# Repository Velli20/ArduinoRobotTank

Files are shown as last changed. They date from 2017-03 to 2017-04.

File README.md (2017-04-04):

# ArduinoRobotTank

CAD Assembly

Fully 3D-printable robot for Arduino Mega/Uno/Due Controller Board. Designed to fit up to 2 pcs of Arduino shields on top of the controller board.

## Parts to print

- Chassis_top.stl
- Chassis_bottom.stl
- Motor_mount_plate.stl (2 pcs)
- Wheel_cover_14_t.stl (2 pcs)
- Track_wheel_14t.stl (6 pcs)
- Motor_cover.stl (2 pcs)
- Tank_link_pin.stl (68 pcs)
- tank_link.stl (68 pcs)
- Front_cover_for_HC_SR04.stl (2 pcs)

## Optional parts to print

- Chassis_fastener_holder.stl (29 pcs). These are for holding chassis nuts in place so it is easier to assemble the robot.

## Fasteners

- ISO10642 Screw M3x8 40 pcs
- ISO14579 Screw M3x12 8 pcs
- ISO14579 Screw M3x25 4 pcs
- ISO4032 Nut M3 46 pcs

## Fasteners for LCD:

- ISO4762 Screw M2x8 4 pcs
- ISO4032 Nut M2 4 pcs

## Fasteners for Ultrasonic HC-SR04 Distance Sensor:

- ISO4762 Screw M2x8 8 pcs
- Nylon Spacers M2x5 8 pcs
- ISO4762 Screw M2x12 8 pcs

## Electronics

- 2x geared DC motors
- Arduino DUE/Mega/UNO Controller Board
- L298P Motor Shield R3
- 7.4 V LiPo battery

## Optional electronics

- ESP8266 WiFI Development Board 
- SSD1306 0.96" I2C 128X64 OLED LCD
- Ultrasonic HC-SR04 Distance Sensor 2 pcs
- HC-05 Bluetooth module 

## Code example

Usage of the skid steering algorithm:

```C++
#define MOTOR_SPEED_MAX 255     // Define max speed
#define MOTOR_SPEED_MIN -255    // Define min speed

SkidSteer skidSteer;

void loop() {
    skidSteer.move(255, 100);   // Move at speed 255 in x direction and 100 at y direction
}
```

## Images

Printed
Printed

## Android app

You can find precompiled apk in Android-App folder. With this app you can create "programs" that can be executed over Bluetooth connection. It also has a serial console and a "joystick" manual control.

Screenshots

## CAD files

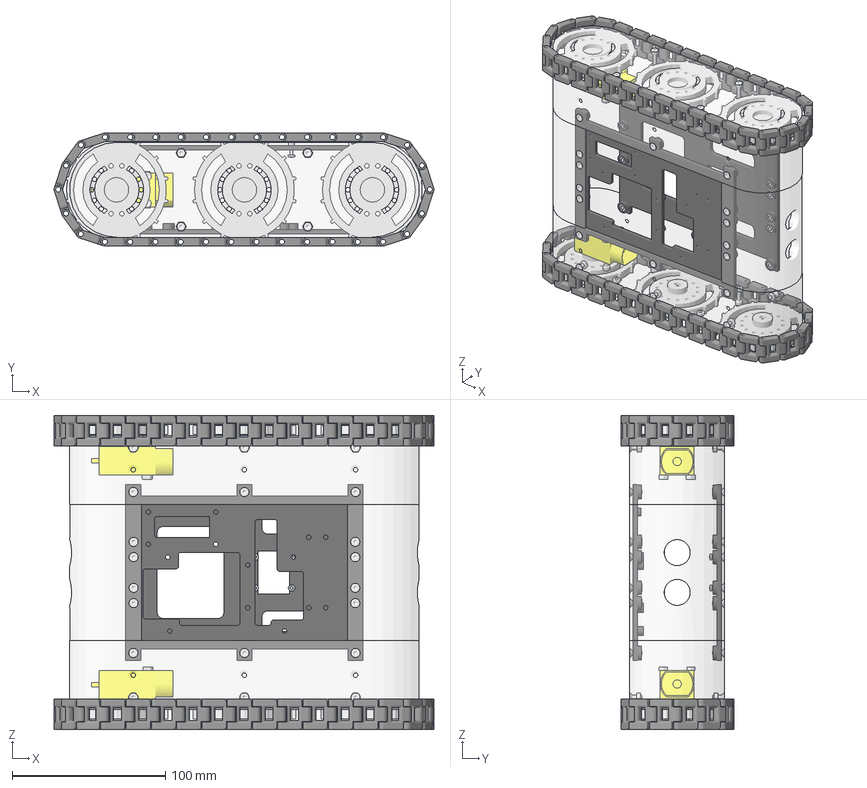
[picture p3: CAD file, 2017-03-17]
Assembly.FCStd
247.9 x 73.8 x 205.0 mm
M3x8-Screw
M3x8-Screw001
M3x8-Screw002
M3x8-Screw003
M3x8-Screw004
M3x8-Screw005
M3-Nut015
M3-Nut014
M3-Nut013
M3-Nut012
M3-Nut011
M3-Nut010
M3-Nut009
M3x12-Screw
M3x12-Screw001
M3x12-Screw002
M3x12-Screw003
M3-Nut008
M3-Nut007
M3-Nut006
M3-Nut002
(M3.5)-Nut020
(M3.5)-Nut019
(M3.5)-Nut018
(M3.5)-Nut017
M3x12-Screw010
M3x12-Screw008
M3x12-Screw007
M3x12-Screw009
M3x25-Screw001
M3x25-Screw
M3-Nut001
M3-Nut
(M3.5)-Nut012
(M3.5)-Nut011
M3x25-Screw003
M3x25-Screw002
(M3.5)-Nut001
(M3.5)-Nut002
M3x8-Screw010
M3x8-Screw009
(M3.5)-Nut
M3x8-Screw006
M3x8-Screw014
(M3.5)-Nut005
(M3.5)-Nut004
(M3.5)-Nut003
M3x8-Screw016
M3x8-Screw015
M3x8-Screw017
M3x8-Screw023
M3x8-Screw022
M3x8-Screw024
M3x8-Screw027
M3x8-Screw028
(M3.5)-Nut008
(M3.5)-Nut007
(M3.5)-Nut006
M3-Nut018
M3-Nut016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

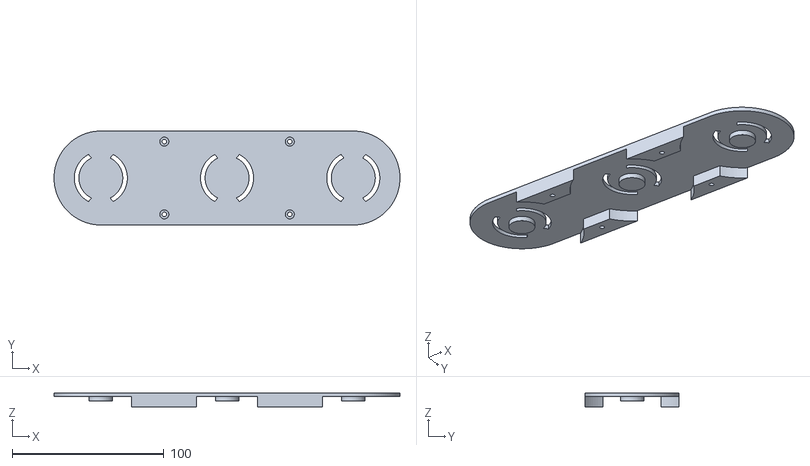
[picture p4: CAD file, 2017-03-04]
STL-files/Wheel_cover_14_t.stl
228.2 x 62.0 x 9.50

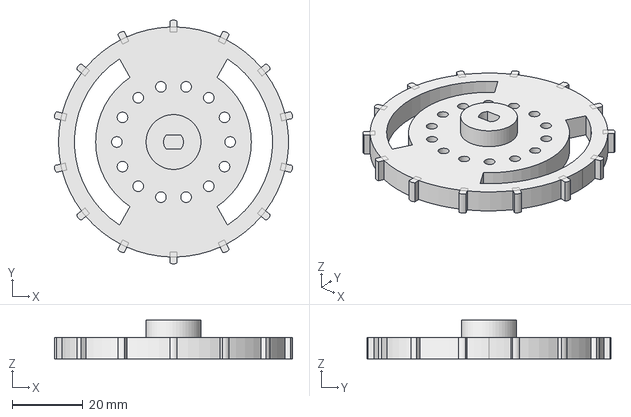
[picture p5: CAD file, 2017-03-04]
CAD-files/Track_wheel_14t_v2.FCStd
67.3 x 68.9 x 11.0 mm

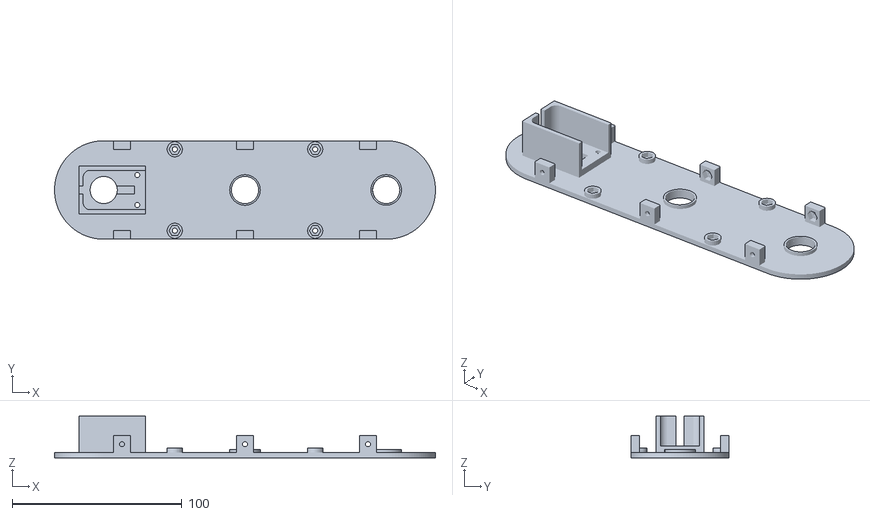
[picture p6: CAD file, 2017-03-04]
STL-files/Motor_mount_plate.stl
224.5 x 58.0 x 24.5

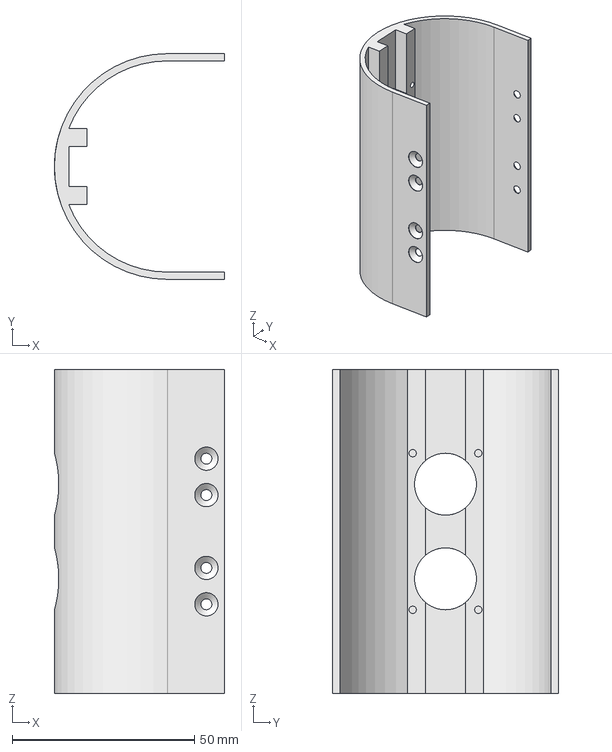
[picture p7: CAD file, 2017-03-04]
CAD-files/Front_cover_with_ultrasonic_distance_sensor_mount.FCStd
46.8 x 62.0 x 89.0 mm

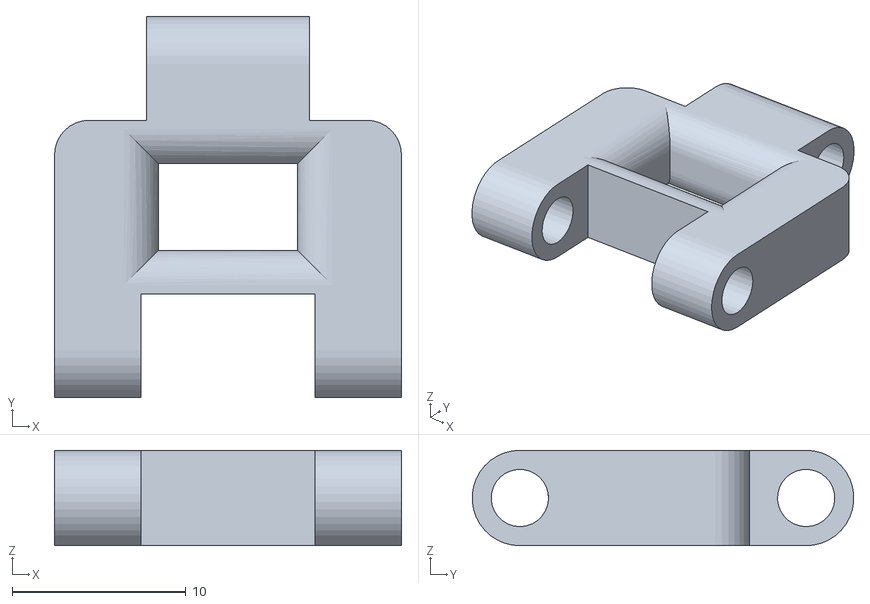
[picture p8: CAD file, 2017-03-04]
STL-files/Tanklink.stl
20.0 x 22.0 x 5.50

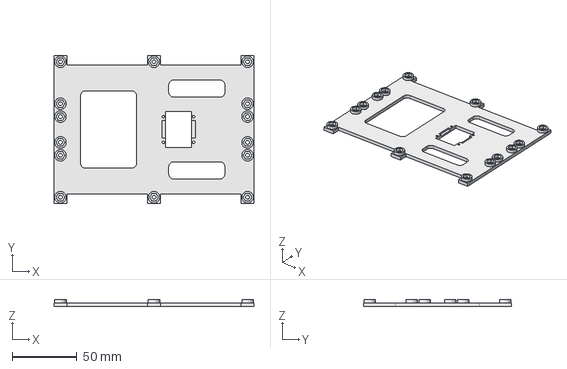
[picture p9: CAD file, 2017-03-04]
CAD-files/Chassis_top.FCStd
155.0 x 115.0 x 5.70 mm

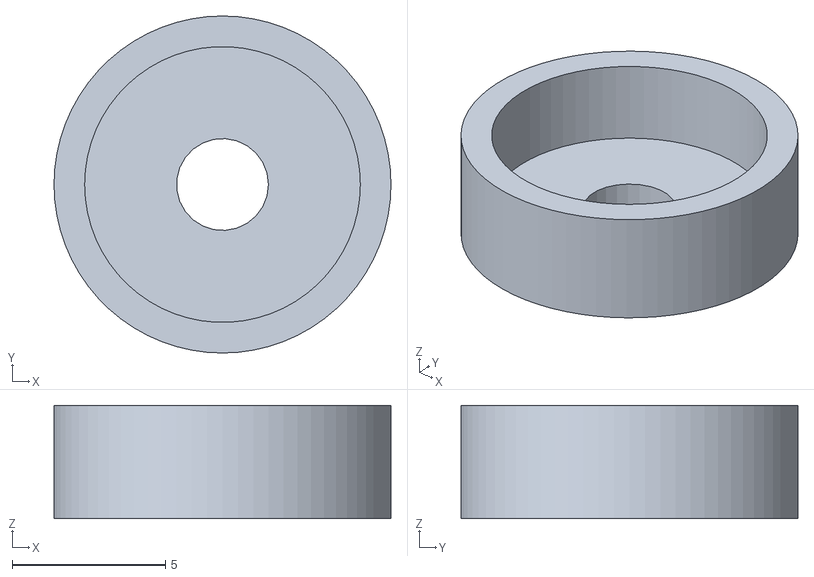
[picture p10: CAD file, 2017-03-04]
STL-files/Chassis_fastener_holder.stl
11.0 x 11.0 x 3.70

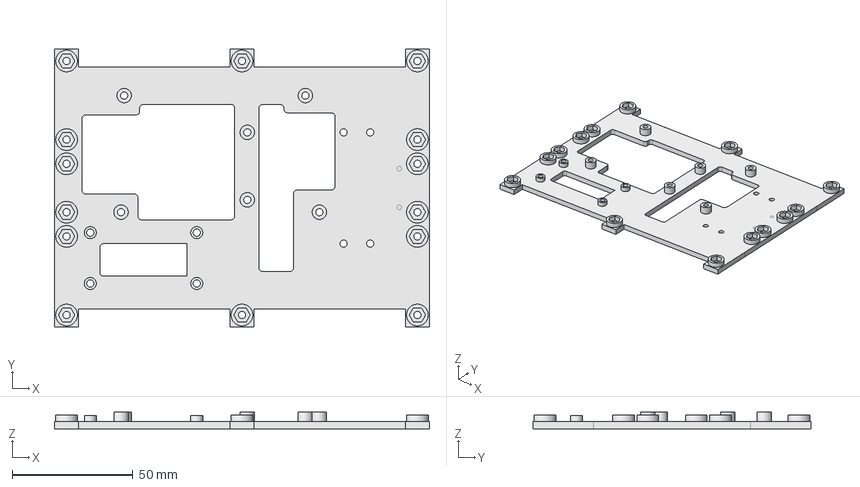
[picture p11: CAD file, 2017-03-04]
CAD-files/Chassis_bottom.FCStd
155.0 x 115.0 x 7.00 mm

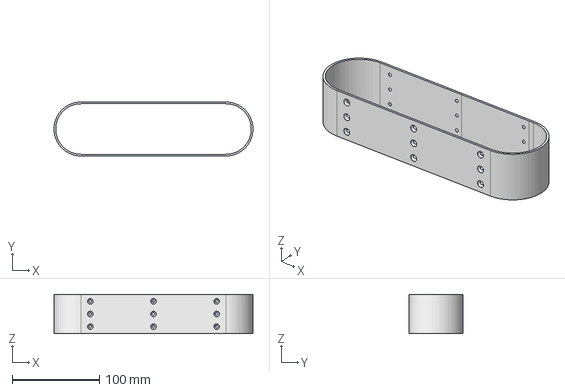
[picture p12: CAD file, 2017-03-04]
CAD-files/Motor_cover.FCStd
228.5 x 62.0 x 45.0 mm

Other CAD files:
CAD-files/Wheel_cover_14_t_v2.FCStd
STL-files/Front_cover_for_HC_SR04.stl
CAD-files/Motor_mount_plate_v2.FCStd
STL-files/Track_wheel_14t.stl
CAD-files/Chassis_nut_holder.FCStd
STL-files/Chassis_bottom.stl
STL-files/Chassis_top.stl
STL-files/Motor_cover.stl

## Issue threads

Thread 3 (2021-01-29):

Question for help

MaxLansing, 2021-01-29:
Hi there,
thx for sharing the project, i'm new to arduino, and i would like to build your rover for the daughter. i have the same parts as per your suggestion, printed all the parts.
But since i am new to the arduino world, and new to programming, i would like to ask if you could share the (working)code with all definitions and maybe a wiring picture if at all possible. At least i could reverse-engineer the mistakes i made and/or see where i am stuck.

thx for great design and the sharing regardless!

Closed 2021-01-30.

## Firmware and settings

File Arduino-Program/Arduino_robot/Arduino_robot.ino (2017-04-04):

#include "skidSteer.h"
#include "configuration.h"
#include <stdio.h>
#include <stdarg.h>


/* Variables */
long lcdLastUpdate = 0;
int speedX = 0;
int speedY = 0;

SkidSteer skidSteer;

/* Function prototypes*/
void updateLCD(void);
void sendResponse(char * response);
void sendResponse(const char * formatter, ...);

/* Put your setup code in this function, to run once: */
void setup() {
  Serial.begin(9600);
  BLUETOOTH_MODULE_SERIAL_PORT.begin(BLUETOOTH_MODULE_BAUD_RATE);
  BLUETOOTH_MODULE_SERIAL_PORT.setTimeout(BLUETOOTH_READ_TIMEOUT);

#ifdef HAS_OLED_LCD
  /* Init OLED display connected at i2c address 0x3C */
  display.begin(SSD1306_SWITCHCAPVCC, 0x3C);
  display.clearDisplay();
  display.setTextSize(1);
  display.setTextColor(WHITE);
#endif /* HAS_OLED_LCD */

  /* Send message to Android console */
  sendResponse("Arduino Tank ready");
  skidSteer.delay(11000);
}

void loop() {

  /* Check if there is data available in Bluetooth Serial Buffer */
  if (BLUETOOTH_MODULE_SERIAL_PORT.available() && !skidSteer.isDelaying()) {
    char command = BLUETOOTH_MODULE_SERIAL_PORT.read();
    long timeReadingStart = millis();
    long value;

    switch (command) {

      /* Commands send by Android app.
         Format: #VALUE where # is the letter prefix and VALUE is an interger 0-255
         Example: X100 == Move in x direction at speed of 100 */

      case 'Y':   /* Command accelerometer tilt in y direction */
      case 'W':   /* Command joystick y-axis*/
        speedY = BLUETOOTH_MODULE_SERIAL_PORT.parseInt();;
        break;

      case 'X':   /* Command accelerometer tilt in x direction */
      case 'A':   /* Command joystick x-axis */
        speedX = BLUETOOTH_MODULE_SERIAL_PORT.parseInt();;
        break;
      case 'D':   /* Command wait or delay */
        value = BLUETOOTH_MODULE_SERIAL_PORT.parseInt();
        sendResponse("Arduino Tank: Delaying for %d ms", value);
        skidSteer.delay(value);
        break;
      case 'N':   /* Command move amount of distance in cm backward */
        value = BLUETOOTH_MODULE_SERIAL_PORT.parseInt();
        sendResponse("Arduino Tank: Moving %d cm backward", value);
        skidSteer.moveDistance((int)value, false);
        break;
      case 'H':   /* Command move amount of distance in cm forward */
        value = BLUETOOTH_MODULE_SERIAL_PORT.parseInt();
        sendResponse("Arduino Tank: Moving %d cm forward", value);
        skidSteer.moveDistance((int)value, true);
        break;
      case 'J':   /* Command rotate counterclockwise amount of degrees */
        value = BLUETOOTH_MODULE_SERIAL_PORT.parseInt();
        sendResponse("Arduino Tank: Rotating %d degrees CCW", value);
        skidSteer.rotate((int)value, true);
        break;
      case 'K':   /* Command rotate clockwise amount of degrees */
        value = BLUETOOTH_MODULE_SERIAL_PORT.parseInt();
        sendResponse("Arduino Tank: Rotating %d degrees CW", 100);
        skidSteer.rotate((int)value, false);
        break;
      case 'S':   /* Command set x speed to 0 and y speed to 0-255 */
        value = BLUETOOTH_MODULE_SERIAL_PORT.parseInt();
        sendResponse("Arduino Tank: Speed set to %d. Max value is set to %d and Min %d", value, MOTOR_SPEED_MAX, MOTOR_SPEED_MIN);
        speedY = value;
        speedX = 0;
        break;
      default:
        sendResponse("Arduino Tank: Unknown command \"%c\"", command);

        break;
    }
  }

  /* Update LCD every 500 ms */
  if (millis() >= (lcdLastUpdate + 100)) {
    updateLCD();
    lcdLastUpdate = millis();
  }

  /* Check that delay function is inactive */
  if (!skidSteer.isDelaying()) {
    skidSteer.move(speedX, speedY);
  }
}




/* Updates content of the OLED LCD if LCD is connected */
void updateLCD() {

#ifdef HAS_OLED_LCD
  char text[40];
  if (skidSteer.isDelaying()) {
    sprintf(text, "Speed Y: %d\nSpeed X: %d\nDelay for: %d ms", speedY, speedX, skidSteer.getRemainingDelayTime());
  } else {
    sprintf(text, "Speed Y: %d\nSpeed X: %d", speedY, speedX);
  }
  display.clearDisplay();
  display.setCursor(0, 5);
  display.print(text);
  display.display();
#endif /* HAS_OLED_LCD */
}

/* Send message to Android App console
   @param formatter: String that contains a format string
   @param values: Additioanl int values reltated to formatter string
*/
void sendResponse(const char * formatter, ...) {
  va_list args;
  va_start(args, formatter);

  char response[80] = {"\0"};
  vsprintf(response, formatter, args);

  BLUETOOTH_MODULE_SERIAL_PORT.write(response);
  BLUETOOTH_MODULE_SERIAL_PORT.write("\r");
  BLUETOOTH_MODULE_SERIAL_PORT.flush();

  va_end(args);

}

/* Send message to Android App console
   @param response: pointer to message to send
*/
void sendResponse(char * response) {
  BLUETOOTH_MODULE_SERIAL_PORT.write(response);
  BLUETOOTH_MODULE_SERIAL_PORT.write("\r");
  BLUETOOTH_MODULE_SERIAL_PORT.flush();
}

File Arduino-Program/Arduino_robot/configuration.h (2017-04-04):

/* Uncomment the following defination if SSD1306 0.96" I2C 128X64 OLED LCD is connected */
/* #define HAS_OLED_LCD */
#define HAS_OLED_LCD
#ifdef  HAS_OLED_LCD
/* Import libraries that are required to communicate with
   the SSD1306 0.96" I2C 128X64 OLED LCD.

   Download the following libraries
   https://github.com/adafruit/Adafruit-GFX-Library
   https://github.com/adafruit/Adafruit_SSD1306
*/
#include <Adafruit_GFX.h>
#include <Adafruit_SSD1306.h>
#include <Wire.h>

#define OLED_RESET 4
Adafruit_SSD1306 display(OLED_RESET);

#endif /* HAS_OLED_LCD */

/* Uncomment the following defination if Ultrasonic HC-SR04 Distance Sensor is connected */
/* #define HAS_ULTRASONIC_DISTANCE_SENSOR */
#ifdef HAS_ULTRASONIC_DISTANCE_SENSOR

/* Import library that is reguired to communicate wit the sensor
   Link to download NewPing library
   http://playground.arduino.cc/Code/NewPing#Download */
#include <NewPing.h>

/* Defines for the ultrasonic distance sensor */
#define PIN_ULTRASONIC_TRIGGER 51                 // Arduino pin tied to trigger pin on the ultrasonic sensor.
#define PIN_ULTRASONIC_ECHO 53                    // Arduino pin tied to echo pin on the ultrasonic sensor.
#define ULTRASONIC_MAX_DISTANCE 200               // Maximum distance we want to ping for (in centimeters)

#endif /* HAS_ULTRASONIC_DISTANCE_SENSOR */

/* Serial port at which bluetooth module is connected.
   Arduino UNO has only one serial port, so change the value to
   Serial and make sure to disconnect the module when uploading the code
   to the Arduino board */
#define BLUETOOTH_MODULE_SERIAL_PORT    Serial2
#define BLUETOOTH_MODULE_BAUD_RATE      57600
#define BLUETOOTH_READ_TIMEOUT          100

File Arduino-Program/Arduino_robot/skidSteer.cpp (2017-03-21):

#include "skidSteer.h"

/* Private code */

/*
 * @brief   LP298P Motor driver initialization prosedure. 
 *          If left or right pwm pin is not defined then
 *          skidSteerInitializationFailed is set to true
 */
void SkidSteer::initialize() {
  
#ifdef PIN_MOTOR_LEFT_DIRECTION || PIN_MOTOR_RIGHT_DIRECTION
  pinMode(PIN_MOTOR_LEFT_DIRECTION, OUTPUT);
  pinMode(PIN_MOTOR_RIGHT_DIRECTION, OUTPUT);
  skidSteerIsReady = true;
#else 
  skidSteerInitializationFailed = true
#endif 

#ifdef PIN_MOTOR_LEFT_BRAKE && PIN_MOTOR_RIGHT_BRAKE
  pinMode(PIN_MOTOR_LEFT_BRAKE, OUTPUT);
  pinMode(PIN_MOTOR_RIGHT_BRAKE, OUTPUT);

  releaseMotorBrakes(true);
#endif

}

/*
 * @brief   Engage the motor brakes by setting positive
 *          DC signal to the motor driver chips brake pins.
 *          This will not work if the traces to the brake inputs 
 *          are cut on the motor shield or brake pins are
 *          undefined.
 */
void SkidSteer::releaseMotorBrakes(boolean releaseBrakes) {
#ifdef PIN_MOTOR_LEFT_BRAKE && PIN_MOTOR_RIGHT_BRAKE
  digitalWrite(PIN_MOTOR_LEFT_BRAKE, releaseBrakes ? LOW : HIGH);
  digitalWrite(PIN_MOTOR_RIGHT_BRAKE, releaseBrakes ? LOW : HIGH);
#endif
}

/* Public code */

/*
 * @brief   Function that calculates left and right motor 
 *          speed based on y and x vectors. Requires that initialization
 *          is passed succesfully
 * @param   y: Speed vector in y direction 
 * @param   x: Speed vector in x direction
 */
void SkidSteer::move(int y, int x) {
  if (!skidSteerIsReady) {
    initialize();
    if(skidSteerInitializationFailed) {
      return;
    }
  } 
  int motorSpeedLeft = x + y;
  int motorSpeedRight = x - y;
  float leftMotorScaled, rightMotorScaled;
  float leftMotorScale, rightMotorScale, maxMotorScale;


  /* Calculate the scale of the results in comparision base 8 bit PWM resolution */
  leftMotorScale =  motorSpeedLeft / 255.0;
  leftMotorScale = abs(leftMotorScale);
  rightMotorScale =  motorSpeedRight / 255.0;
  rightMotorScale = abs(rightMotorScale);

  /* Choose the max scale value if it is above 1 */
  maxMotorScale = max(leftMotorScale, rightMotorScale);
  maxMotorScale = max(1, maxMotorScale);

  /* And apply it to the mixed values */
  leftMotorScaled = constrain(motorSpeedLeft / maxMotorScale, -255, 255);
  rightMotorScaled = constrain(motorSpeedRight / maxMotorScale, -255, 255);

  digitalWrite(PIN_MOTOR_LEFT_DIRECTION, !(leftMotorScaled > 0));
  digitalWrite(PIN_MOTOR_RIGHT_DIRECTION, !(rightMotorScaled > 0));

  analogWrite(PIN_MOTOR_LEFT_SPEED, leftMotorScaled < 0 ? leftMotorScaled * -1 : leftMotorScaled);
  analogWrite(PIN_MOTOR_RIGHT_SPEED, rightMotorScaled < 0 ? rightMotorScaled * -1 : rightMotorScaled);
}

/* 
 * @brief   Halts the robot movement by sending zero width pwm pulse
 *          to motor driver chip. No quarantees that robot will
 *          actually stop. To engage brakes 
 *          call releaseMotorBrakes(false) function
 */
void SkidSteer::stop() {
  analogWrite(PIN_MOTOR_LEFT_SPEED, 0);
  analogWrite(PIN_MOTOR_RIGHT_SPEED, 0);

}

/* 
 * @brief   A non blocking delay function. This wont stop
 *          main loop to excecuting the program and will not notify
 *          when then delay is complete. There are also no guarantees
 *          that delayed time is exactly the time is requested to delay.
 * @param   timesInMillis: Amount of time in milliseconds to delay
 */
void SkidSteer::delay(long timeInMillis) {
  delayUntil = millis() + timeInMillis;
}

/* 
 * @brief   Function to check if rquested delay time is  passed
 * @retval  return true if delay is complete
 */
boolean SkidSteer::isDelaying() {
  return (millis() < delayUntil);
}

/* @brief   
   @retval  Returns amount of milliseconds to delay */
long SkidSteer::getRemainingDelayTime() {
  return delayUntil - millis();
}

/* 
 * @brief   Move amount of distance in cm basing on feedback 
 *          coming from the motor sensor (i.g pulse sensor)
 * @param   distanceInCm: Distance to move in cm
 * @param   forward: Direction of the movement.
 *          True if forward false if backward
 */
void SkidSteer::moveDistance(int distanceInCm, boolean forward) {
#ifdef MOTOR_TYPE_STEPPER_MOTOR
    /* TODO */
#elif HAS_MOTOR_FEEDBACK_SENSOR
    /* TODO */
#else 
    /* No feedback sensor connected. Use timers to move distance approximately */
    int deltaTime = distanceInCm * 1000; // Lets assume that it takes one second to move one cm
    
  
#endif
}

/*
 * @brief   Rotate amount of degrees either counterclockwise or clockwise
 *          basing on the feedback coming from the accelerometer sensor.
 * @param   degreesToRotate: amount of degrees to rotate 
 * @param   CCW: Rotation direction. True if counterclockwise, else false
 */
void SkidSteer::rotate(int degreesToRotate, boolean CCW) {
  
}

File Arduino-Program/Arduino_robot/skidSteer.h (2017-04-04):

#ifndef SKID_STEER_H
#define SKID_STEER_H

#include <Arduino.h> 

#define MOTOR_SPEED_MAX 255
#define MOTOR_SPEED_MIN -255

/* Defines for the motor shield channel A */
#define PIN_MOTOR_LEFT_DIRECTION 12
#define PIN_MOTOR_LEFT_BRAKE 9
#define PIN_MOTOR_LEFT_SPEED 3

/* Defines for the motor shield channel B */
#define PIN_MOTOR_RIGHT_DIRECTION 13
#define PIN_MOTOR_RIGHT_BRAKE 8
#define PIN_MOTOR_RIGHT_SPEED 11


class SkidSteer {
  private:
    /* Variables */
    bool skidSteerIsReady = false;
    bool skidSteerInitializationFailed = false;
    long delayUntil = 0;
    
    /* Private function prototypes */
    void initialize();
    void releaseMotorBrakes(boolean releaseBrakes);

  public:
    /* Public function prototypes */
    void move(int y, int x);
    void stop();
    void delay(long timeInMillis);
    void moveDistance(int distanceInCm, boolean forward);
    void rotate(int degreesToRotate, boolean CCW);

    boolean isDelaying();
    long getRemainingDelayTime();
};



#endif /*SKID_STEER_H*/
